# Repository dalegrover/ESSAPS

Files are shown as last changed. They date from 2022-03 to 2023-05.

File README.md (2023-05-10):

# ESSAPS: Experimental Small-Scale Anodizing Power Supply
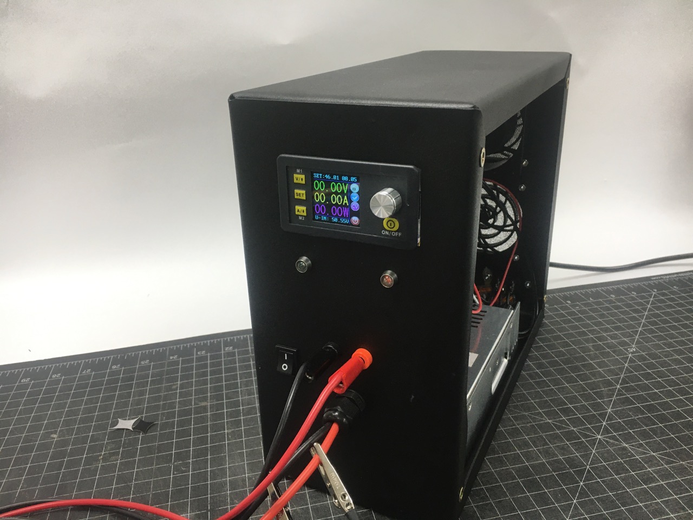
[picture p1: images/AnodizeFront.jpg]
Anodizing power supply front view

The goal of this project is to create an automated power supply to support small-scale anodizing.  By “small-scale”, the output is in the range of 10-15A; this is sufficient for anodizing surfaces of around 1 ft^2 at 12 ASF (amp per sq. ft), or up to around 3 ft^2 at “low current density” (LCD) rates of about 4.5 ASF.
The user interface is via a web page served over WiFi.  The pages are simple HTML--no Javascript, etc.

The power supply is automated and performs the following:
* Given ASF, surface area, ramp time, and target thickness, calculates current, total time, estimated peak voltage, and estimated peak resistance.
* Ramps up the constant current to the target current.
* Stops the current and signals the operator if the time is up or (if enabled) a decrease in resistance is detected (i.e., peak anodizing resistance or PAR).  The latter has been claimed by some to provide a much more reliable method of maximizing layer thickness independent of electrolyte condition, temperature, etc.
* Generates plots in real time of the voltage and current.
* Generates numeric data points for voltage and current (can be copied to a spreadsheet for analysis or plotting).
* By adding a large-valued capacitor and a few low-cost components, the power supply can act as a wire-bonder for bonding aluminum wire to objects to be anodized (i.e., Capacitor-Discharge Welding or CDW, also known in some circles as "sput welding").

This device doesn't do anything that a constant-current power supply plus an attentive person with a calculator can't do.  But, it will do the ramping, timing, and peak resistance detection autonomously, freeing the operator to do other things.

The hardware components of this power supply are:
* 10-15A, 24-50V fixed or variable voltage switching power supply.  A popular brand would be "Mean Well".   24V is likely just sufficient for just anodizing; 48-50V is useful if wire-bonding will be used.
* DPS5015 or DPS5020 Constant-Current/Constant-Voltage buck regulator.  Make sure it supports communication (sometimes sold with a USB converter or Bluetooth, though neither adapter is used for this project).  The DPS3012 will not work--it does not apparently support ModBus.
* ESP-WROOM-32 module.  Make sure the metal shield says "ESP-WROOM-32"--other versions may not work with this code.
* JST-GH 1.25mm 4-pin female cable
* If CDW is desired, a large value (i.e., 0.1 F or more) electrolytic capacitor rated at least 5-10V more than the maximum power supply output, plus a dual relay module.
* Wire, Mini-PV connectors ("DuPont"), AC power switch, circuit breaker, enclosure, fan, fan filters, banana connectors, etc.

The hardware is in a good state.  The software is usable, but needs improvement.

Warning:  This process involves powerful chemicals, high voltage, and the discharge of very high current.  It is critical to use all appropriate safety measures when using this device and process.  The author is not a professional anodizer and may be unaware of other hazards.  Consult a professional before using.  Any use is at your own risk.

See the project wiki for more details:  https://github.com/dalegrover/ESSAPS/wiki

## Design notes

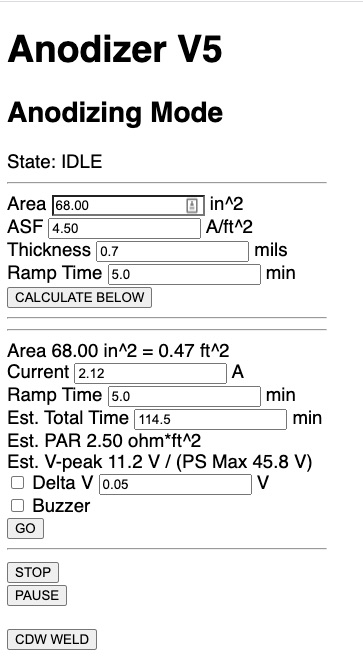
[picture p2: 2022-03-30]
images/webStartPage.jpg

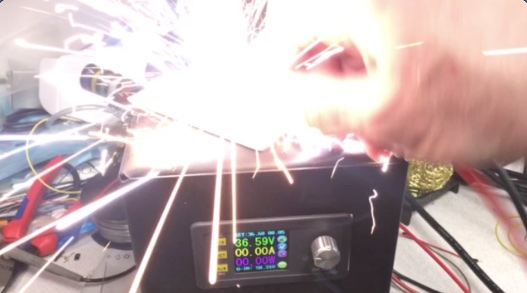
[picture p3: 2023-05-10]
images/CDWThumb.jpg

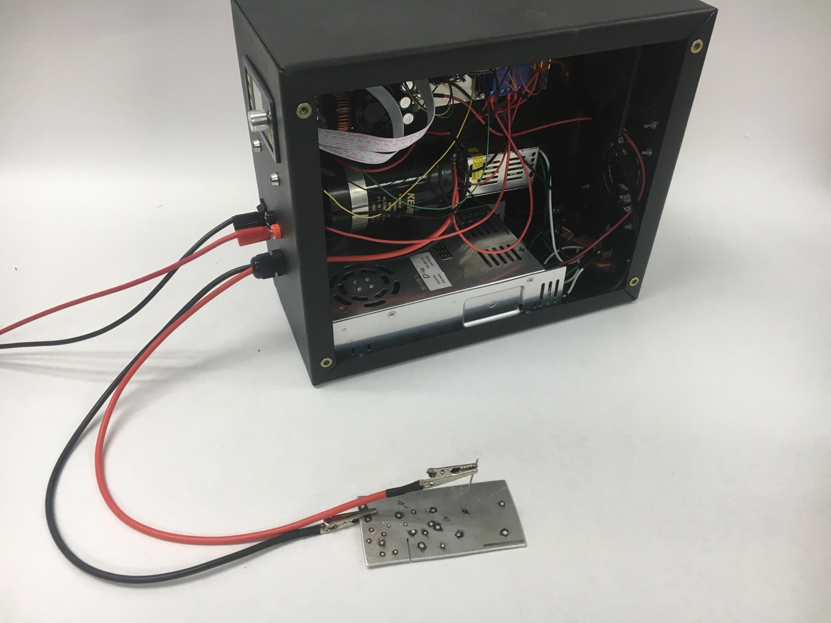
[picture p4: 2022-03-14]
images/AnodizeCDW.jpg

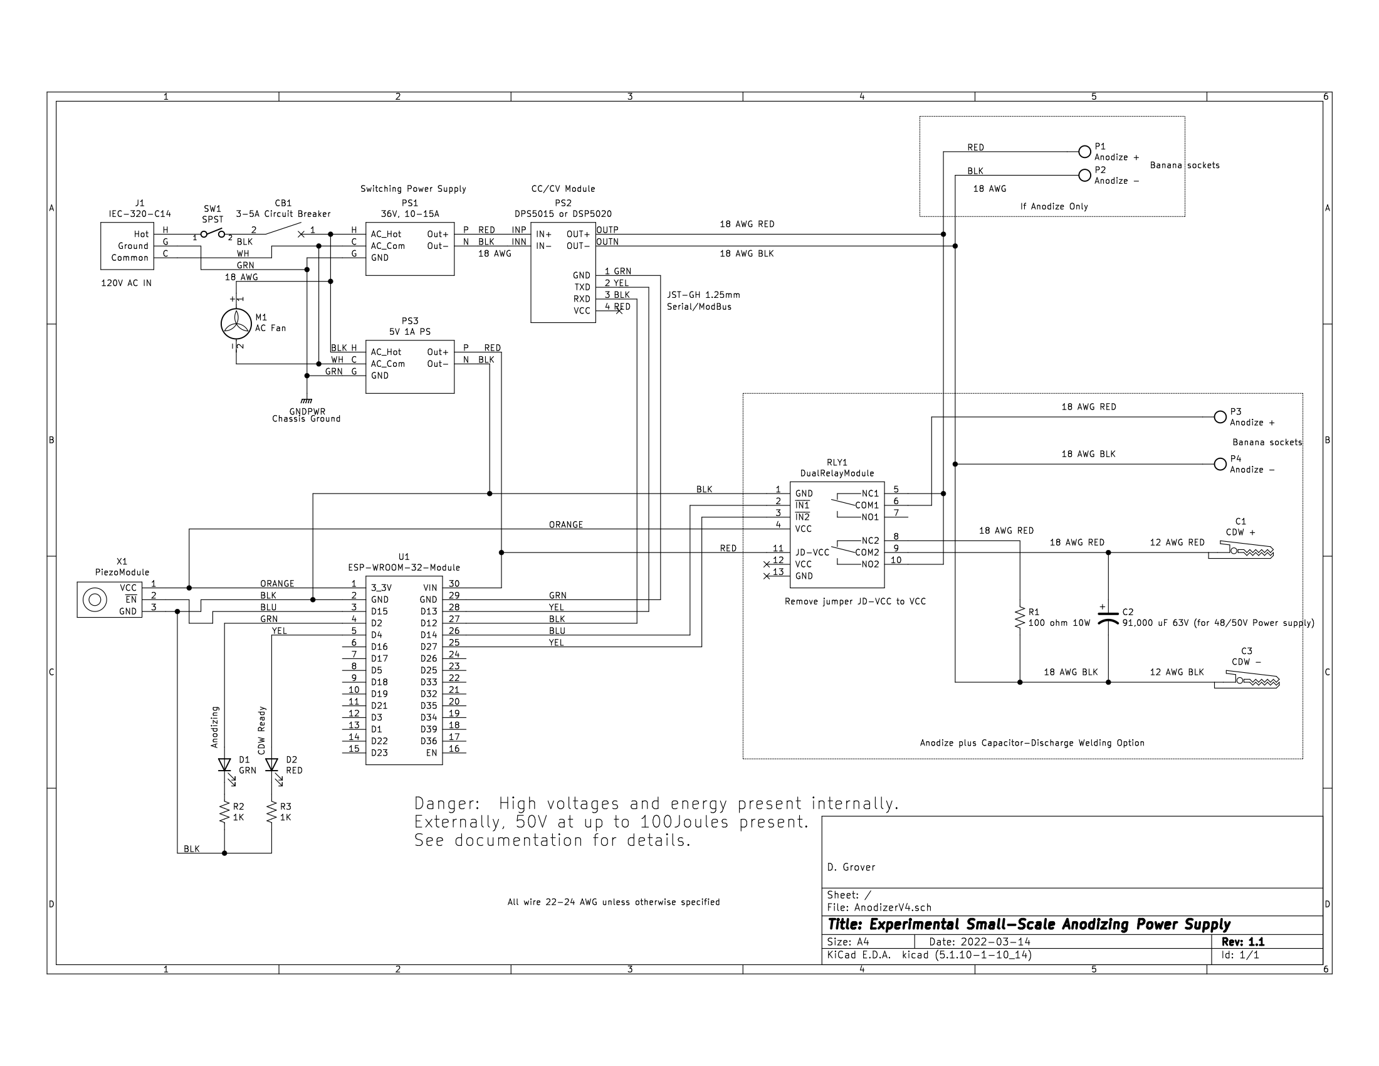
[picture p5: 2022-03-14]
images/AnodizerV4.png

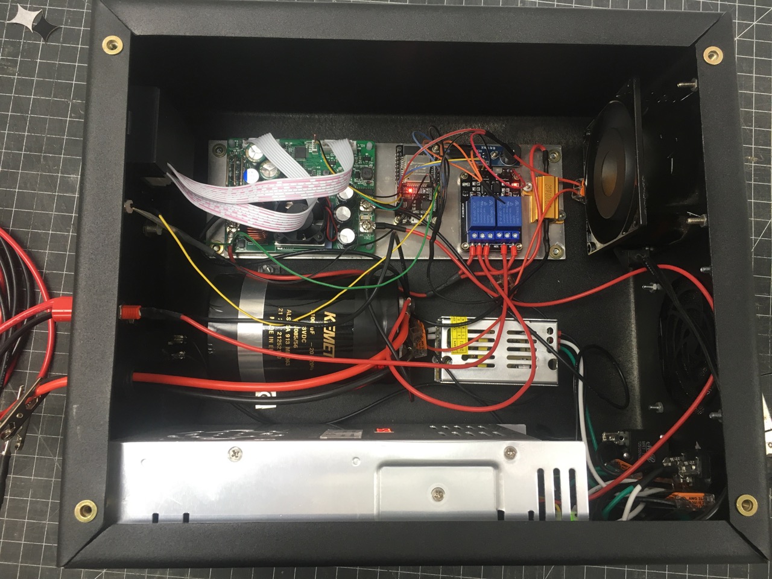
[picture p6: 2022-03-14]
images/AnodizeInside.jpg

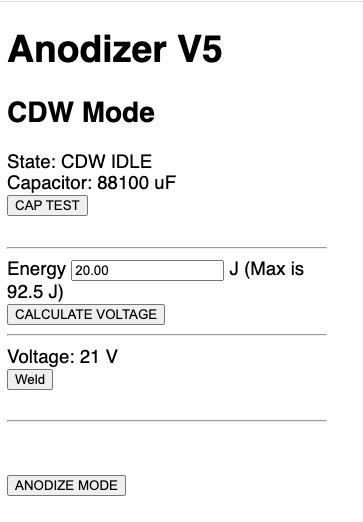
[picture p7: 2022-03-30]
images/webCDWPage.jpg

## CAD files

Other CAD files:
images/Anodizer Enclosure V1 v21.f3d

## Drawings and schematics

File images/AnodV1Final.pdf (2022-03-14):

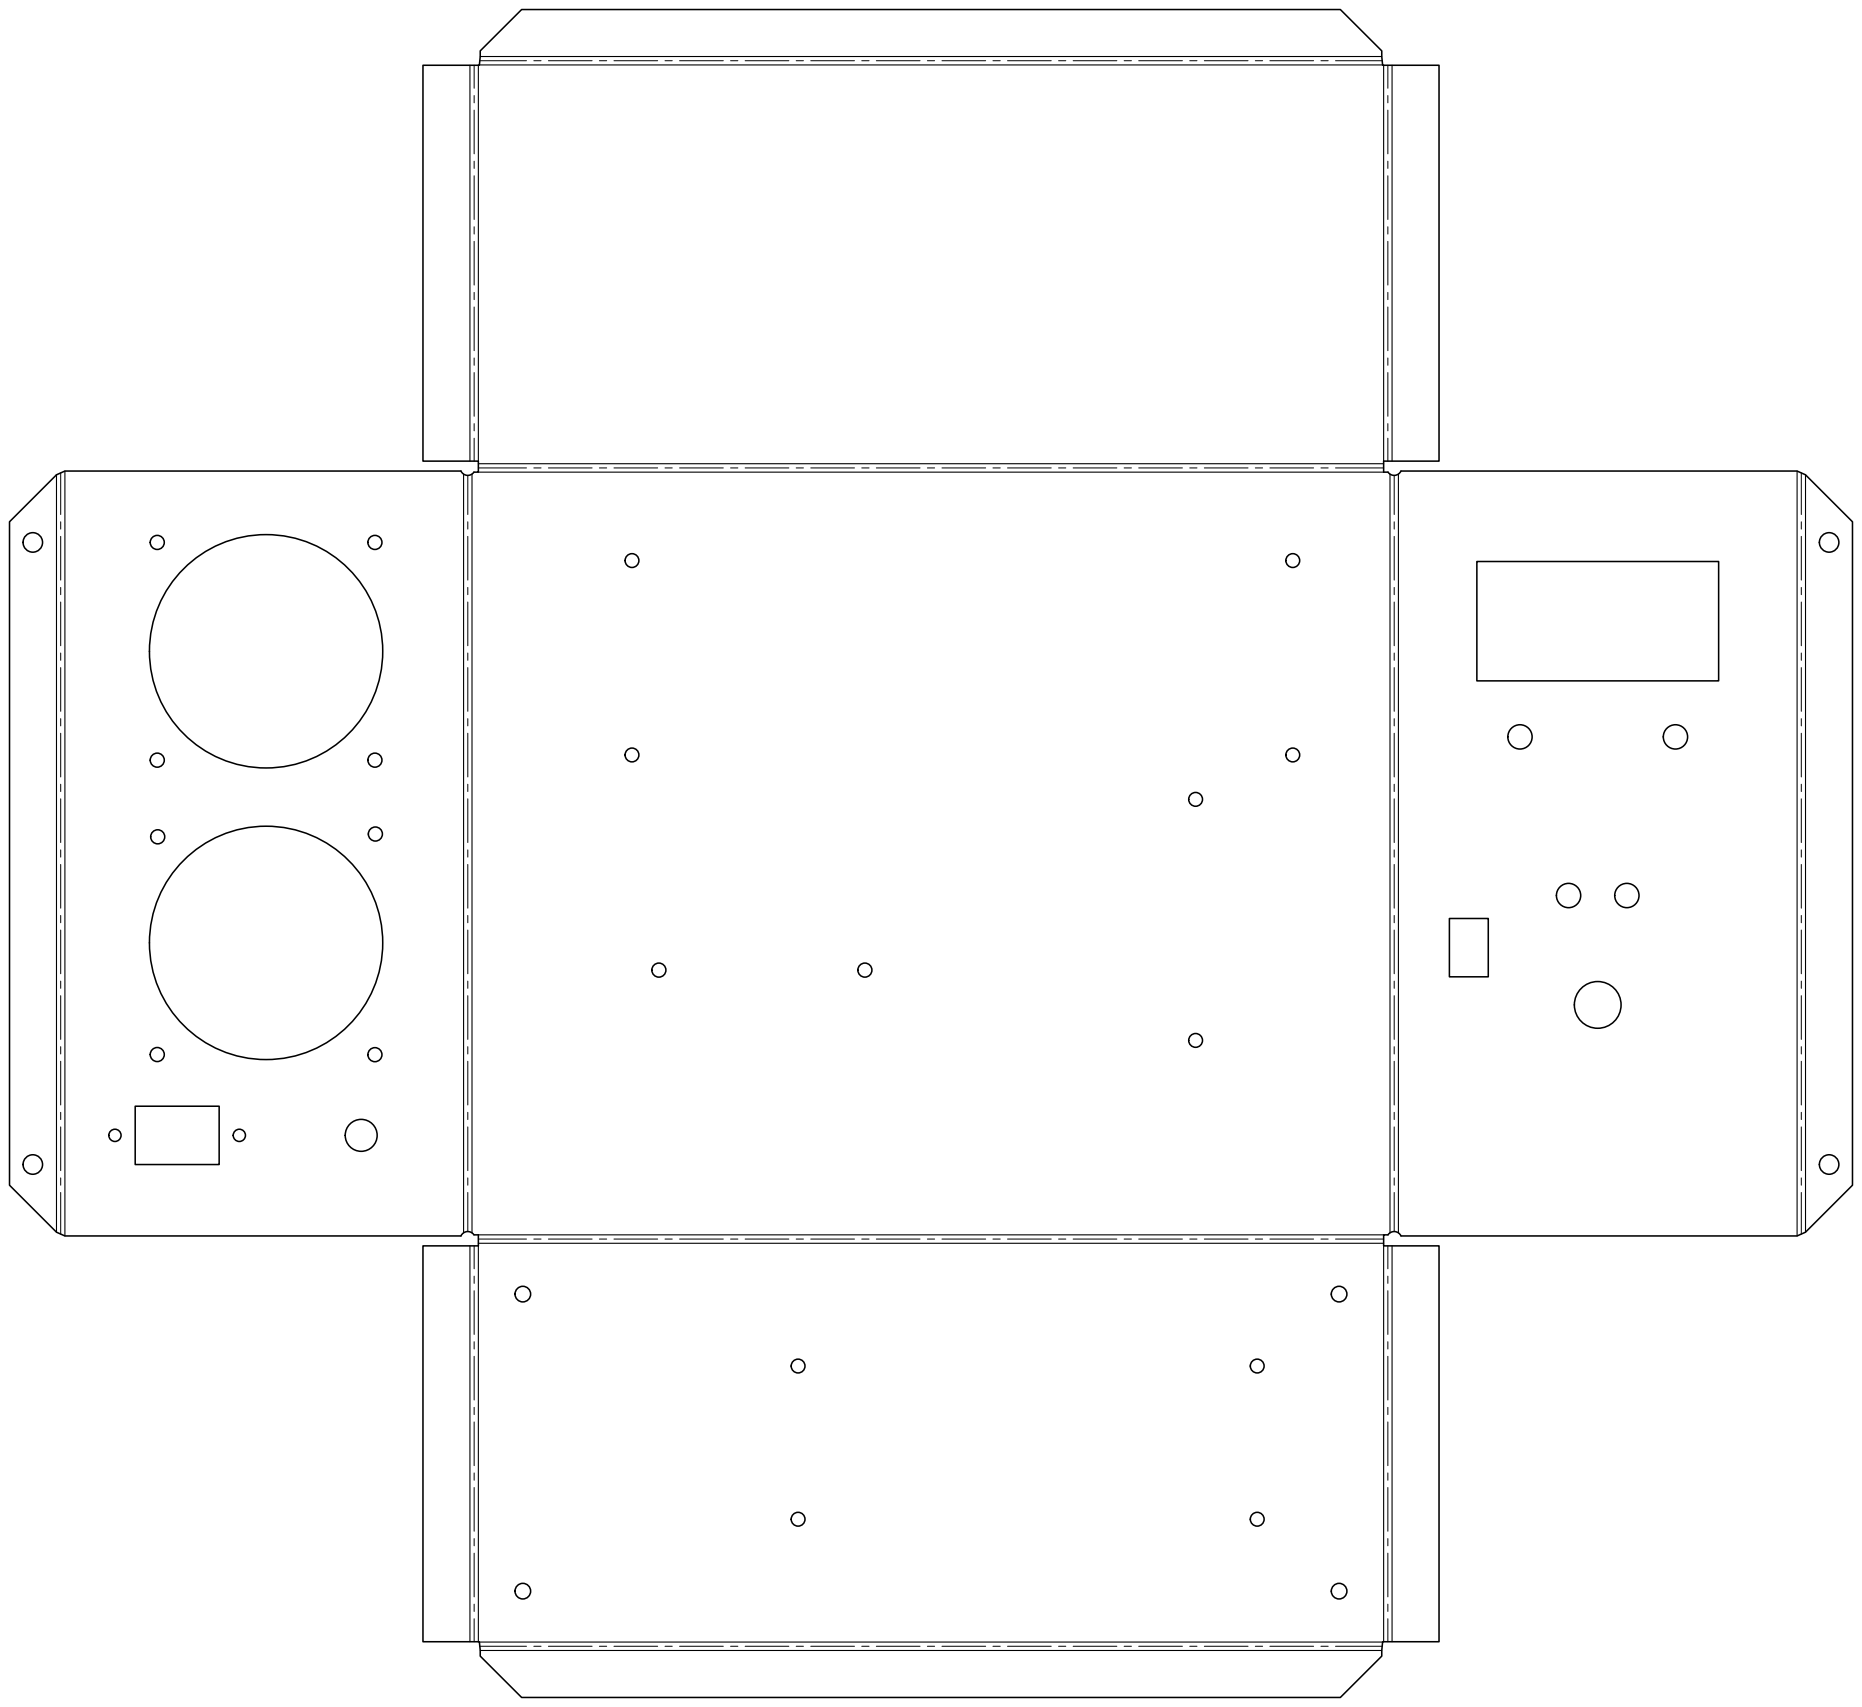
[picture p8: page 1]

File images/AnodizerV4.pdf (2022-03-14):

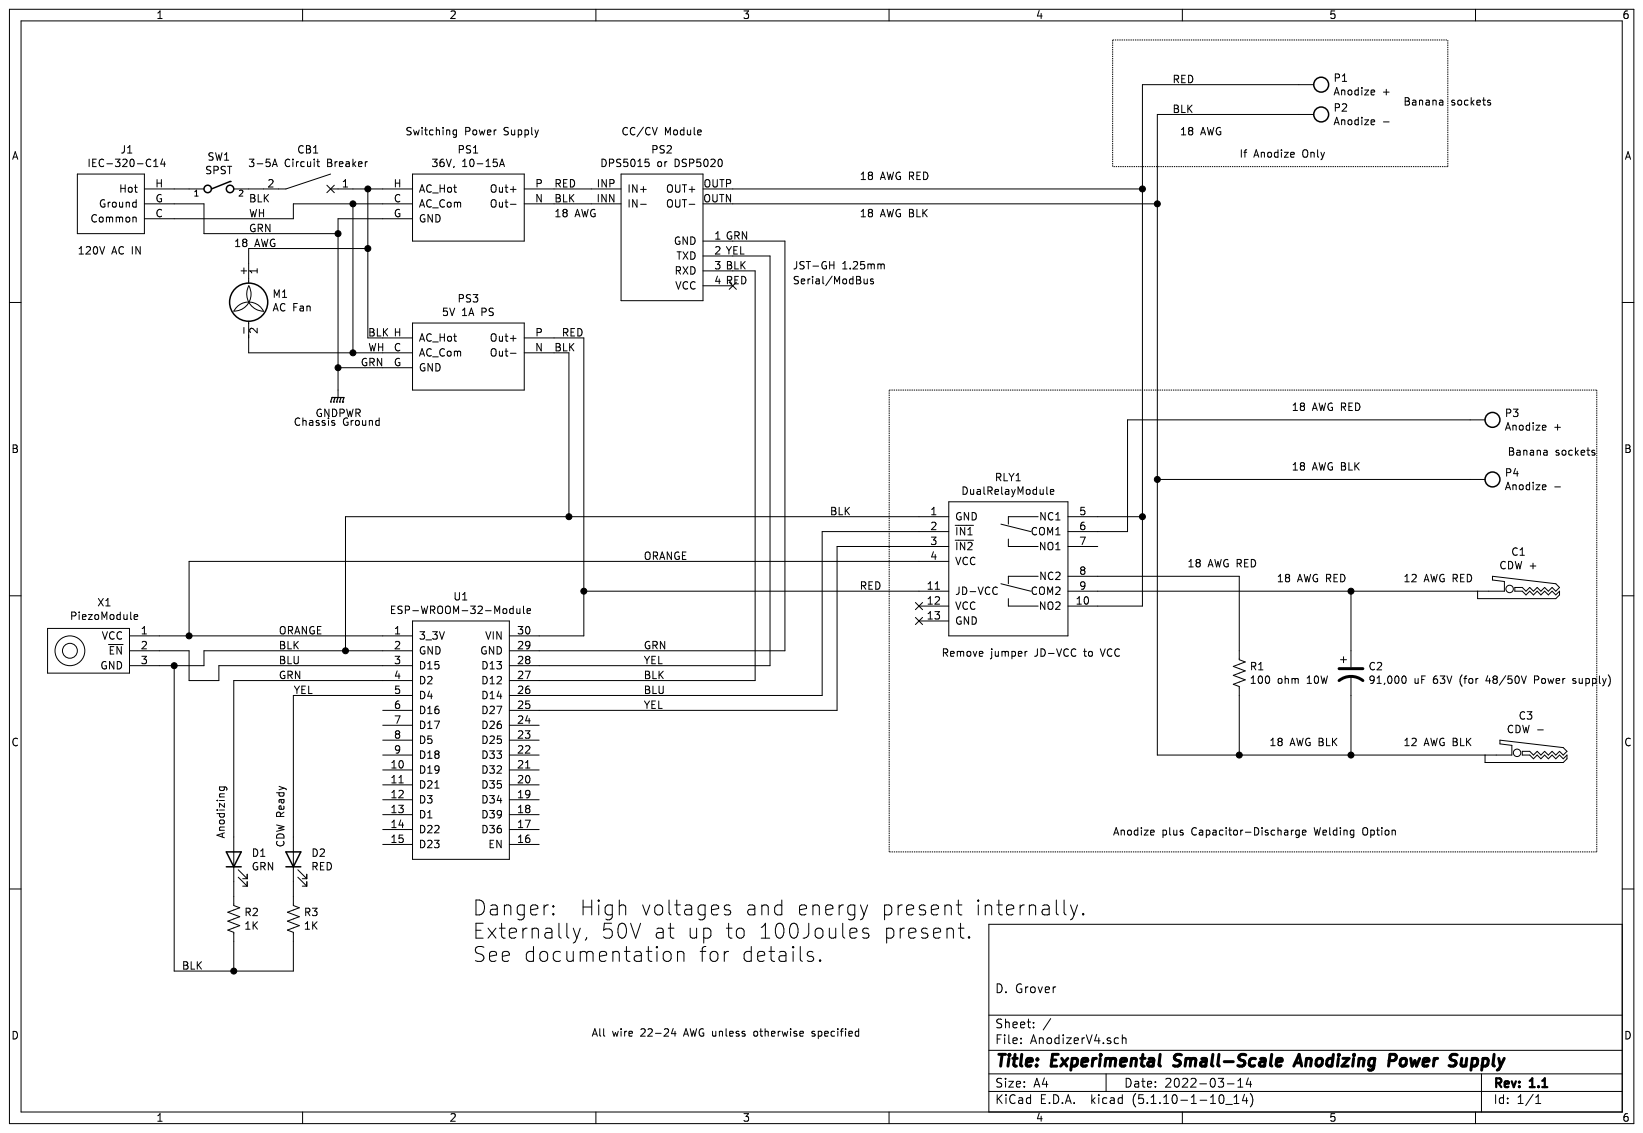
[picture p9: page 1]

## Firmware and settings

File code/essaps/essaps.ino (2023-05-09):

// ESSAPS
// Experimental Small-Scale Anodizing Power Supply
// 5.2
//
// Anodizing power supply and capacitor-discharge welder
// For ESP-WROOM-32 module connected to DPS5015 power supply
// w/ maximum of 50V 15A switching power supply
// Uses ModBus over TTL serial to talk to DPS5015
// TX2 is GPIO 12
// RX2 is GPIO 13
//
// Other I/O:
// GPIO 15:  piezo alarm, active low
// GPIO 2:  Green LED (anodizing active), active high
// GPIO 4:  Red LED (CDW ready to use), active high
// GPIO 13:  RX2 to TXD of DPS5015
// GPIO 12:  TX2 to RXD of DPS5015
// GPIO 14:  relay 1, active low
// GPIO 27:  relay 2, active low

// Relay 1:  hi (default, off) = +Anodize banana socket connected to DPS5015 output
//           lo (active low)   = +Anodize disconnected

// Relay 2:  hi (default, off) = CDW capacitor is discharged through 100 ohm 25W resistor
//           low (active low)  = CDW capacitor is connected to DPS5015 output

// Other connections
// VIN:  +5V in
// GND:  GND
// 3_3V:  Piezo VCC, Relay VCC (remove jumper JD-VCC to VCC, connect +5V to JD-VCC)

//
//  to do:
// if power supply not on, detect and note on web page
// add filtering to the maximum voltage and peak resistance calculation to remove any noise
// ability to save settings (incl. capacitor value)
// make delta v enable persistant, like buzzer
// remove CDW button unless idle/stop/etc.
// more space between buttons & checkboxes
// bold dynamic values


//    Copyright (C) 2021 Dale Grover
//
//
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



#include <WiFi.h>
#include <WebServer.h>

#include "DPS5015.h"

// for debugging without connecting to an actual DPS unit,
// set NO_DPS in DPS5015.h

const char* progVersion = "5.3";

// SSID & Password
const char* ssid = "Anodizer5";  // Enter the SSID here for this device
const char* password = "987654321";  //Enter the password to log on to this device

// IP Address details
IPAddress local_ip(192, 168, 1, 1);
IPAddress gateway(192, 168, 1, 1);
IPAddress subnet(255, 255, 255, 0);

WebServer server(80);  // Object of WebServer(HTTP port, 80 is defult)

float anodizingAreaIn; // area in sq inches, all surfaces
float anodizingAreaFt; // anodizingAreaIn / 144, in sq ft
float anodizingCurrent; // 0.050A to 15A, float
float anodizingRampTime; // minutes
float anodizingMaxTime; // minutes
float anodizingPAR; // peak anodizing resistance (ohm sq ft)
float anodizingVPeak; // Volts, estimated peak voltage
float anodizingASF; // amp/sq ft
float anodizingThickness; // mils
float anodizingPeakRSF; // peak resistance per sq ft
float anodizingDeltaV; // change in V to signal end of cycle
int anodizingEnableDeltaV; // true or false to enable delta V end of cycle
float anodizingMaxV; // actual maximum voltage so far during CC

// CDW welding
float CDWCapacitance; // capacitance in Farads
float CDWEnergy; // energy per weld in Joules
float CDWVoltage; // voltage to give CDWEnergy given CDWCapacitance

// web page status string
char *statusString; // points to a status string--e.g., "Timed out"
char statusBuffer[50]; // in case you need a dynamic status--like "Delta V at 32.7 seconds"
char timeBuffer[20]; // for time, for above

int piezoEnable; // enable buzzer at end of anodizing cycle

// set max voltage to about 5 volts less than input voltage to DPS5015
float maxVoltage;

// second UART (to DPS5015 using modbus)
#define RXD2 13
#define TXD2 12

// piezo buzzer (active, active low) on GPIO15
#define PIEZO 15
#define PIEZO_OFF 1
#define PIEZO_ON 0

// LEDs
#define LED_ANODIZE 2
#define LED_CDW 4
#define LED_ON 1
#define LED_OFF 0

// relays
#define RELAY_1 14
#define RELAY_2 27
#define RELAY_ON 0
#define RELAY_OFF 1

#define BUFLEN 50


// States
#define STATE_IDLE 0
#define STATE_START 1
#define STATE_PAUSE 2
#define STATE_PAUSED 3
#define STATE_RAMP 4
#define STATE_CC 5
#define STATE_DONE 6
#define STATE_TIMED_OUT 7
#define STATE_STOP 8
#define STATE_STOPPED 9
#define STATE_DELTA_V 10
#define STATE_CDW_IDLE 11
#define STATE_TEST_CAP 12
#define STATE_CDW_STOP 13
#define STATE_CDW_CHARGE 14
#define STATE_CDW_CHARGING 15
#define STATE_CDW_READY 16
#define STATE_CDW_WAIT_TO_RESET 17


char *stateNames[] = {"IDLE", "START", "PAUSE", "PAUSED", "RAMP", "CONSTANT CURRENT", "DONE", \
                      "TIMED OUT", "STOP", "STOPPED", "DELTA-V HALT", "CDW IDLE", "TEST CAP", \
                      "CDW STOP", "CDW CHARGE", "CDW CHARGING", "CDW READY", "CDW WAIT TO RESET" \
                     };

int state;
int pauseState;

// data arrays, for 3 hours at 12 samples/minute (5 secs/sample)
#define ARRAY_HOURS 3
#define ARRAY_SAMPLES_PER_MINUTE 12
#define MAX_READINGS (ARRAY_HOURS * 60 * ARRAY_SAMPLES_PER_MINUTE)
float readingsCurrent[MAX_READINGS];
float readingsVoltage[MAX_READINGS];
int readingIndex;

void setup()
{
  // set up piezo
  pinMode(PIEZO, OUTPUT);
  digitalWrite(PIEZO, PIEZO_OFF);

  // set up LEDs
  pinMode(LED_ANODIZE, OUTPUT);
  pinMode(LED_CDW, OUTPUT);
  digitalWrite(LED_ANODIZE, LED_OFF);
  digitalWrite(LED_CDW, LED_OFF);

  // set up relays
  pinMode(RELAY_1, OUTPUT);
  pinMode(RELAY_2, OUTPUT);
  digitalWrite(RELAY_1, RELAY_ON); // disconnect anodize socket
  digitalWrite(RELAY_2, RELAY_OFF); // discharge CDW capacitor

  // serial via USB to host computer
  Serial.begin(115200);
  // serial to DSP5015 power supply (modbus)
  // factory default is 9600, can go to 19200
  Serial2.begin(9600, SERIAL_8N1, RXD2, TXD2);

  delay(4000); // let things settle (was 5000)

  // set to defaults, disable outputs
  setModBusRegVerified(REG_ONOFF_SET, 0); // 0=off, disable output
  // now calculate maximum output voltage, which is Vout = Vin/1.1
  maxVoltage = getModBusReg(REG_VIN_READ) / 100.0 / 1.1;
  setModBusRegVerified(REG_V_SET, int(maxVoltage * 100)); // set MAX_VOLTAGE * 100
  setModBusRegVerified(REG_I_SET, 5); // set 00.05A, minimal current

  // set up web server
  // Create SoftAP
  WiFi.disconnect(); // these 3 lines important:  https://github.com/espressif/arduino-esp32/issues/2025
  WiFi.mode(WIFI_OFF);
  delay(1000);
  WiFi.persistent(false);
  WiFi.softAP(ssid, password);
  delay(2000); // this delay is "very important"--bug in kernal?
  WiFi.softAPConfig(local_ip, gateway, subnet);

  Serial.print("\n\n----------------\nAnodizer v");
  Serial.print(progVersion);
  Serial.print("\n----------------\n");
  Serial.print("Access point: ");
  Serial.println(ssid);
  Serial.println(password);

  Serial.print("Maximum Voltage:  ");
  Serial.println(maxVoltage);

  // we only serve two things: the main page and the svg plot
  server.on("/", handle_root);
  server.on("/graph.svg", graphvi);
  server.onNotFound(handleNotFound);

  server.begin();
  Serial.println("HTTP server started");

  state = STATE_IDLE;
  statusString = "Idle";

  // defaults
  anodizingAreaIn = 144.0; // area in inches (total, all surfaces/sides)
  anodizingASF = 4.5; // for LCD (low current density anodizing), 6 ASF and below
  anodizingThickness = 0.7; // 0.0007" = 0.7 mils thickness
  anodizingRampTime = 5; // default ramp time in minutes
  anodizingDeltaV = 0.05; // change in V to halt cycle (if enabled)
  anodizingEnableDeltaV = false;
  calculateParams();

  // CDW capacitor--this is default, but can test and set programmatically too
  CDWCapacitance = 0.091; // 91,000 uF
  CDWEnergy = 20.0; // 20J, default energy per weld
  calculateCDWVoltage();

  // Energy in CDW capacitor is 1/2 C V^2
  // For 45V and 90,000 uF (0.09F), E=91J.
  // (It so happens that at 45V, E in J is the C in MFD)

  piezoEnable = false; // no buzzer at end by default
  digitalWrite(PIEZO, PIEZO_OFF);

} // setup()


// given area, ASF, thickness, and ramp time, calculate
// current, time, est PAR, est VPeak

// This array maps ASF to PAR
// May need adjusting for sodium bifsulfate; may not be accurate.
// Some folks just use 0.95 ohm for everything, but I believe that may apply at high ASF
// 0 to 24 ASF
float ASFtoPAR[] = {5.00, 4.00, 3.00, 2.67, 2.50, 2.33, 2.17, 2.09, 2.00, 1.92, 1.84, 1.75, 1.67, 1.61, 1.55, 1.49, 1.43, 1.37, 1.31, 1.25, 1.19, 1.13, 1.07, 1.01, 0.95};

void calculateParams()
{
  // convert to sq feet
  anodizingAreaFt = anodizingAreaIn / 144.0;

  // find current
  anodizingCurrent = anodizingAreaFt * anodizingASF;

  // find approx peak anodizing resistance
  if ( anodizingASF > 23.0)
    anodizingASF = 23.0;
  anodizingPAR = ASFtoPAR[ (int) anodizingASF ];

  // find est. peak voltage
  anodizingVPeak = anodizingPAR * anodizingASF;

  // find time, in minutes ("720 rule")
  anodizingMaxTime = 720.0 * anodizingThickness / anodizingASF;
  // ramp time is on average 1/2 current, so add 1/2 ramp time
  anodizingMaxTime += anodizingRampTime / 2;
}


// given capacitance & energy, find voltage required
void calculateCDWVoltage()
{
  CDWVoltage = sqrt( CDWEnergy * 2 / CDWCapacitance);
  if (CDWVoltage > maxVoltage)
  {
    // requested energy requires too high voltage; drop down to maxVoltage
    CDWVoltage = maxVoltage;
    CDWEnergy = CDWCapacitance * CDWVoltage * CDWVoltage / 2.0;
  }
}

float startTime;  // in seconds (converted from millis)
int lastTime; // seconds, in int, last time through



// log readings to arrays
void logReadings(void)
{
  float voltage, current;
  float currentTime;

  // check if time for record sample
  currentTime = getSeconds();
  if ( ((int)currentTime == lastTime) || ( (int)currentTime % 5 != 0) )
  {
    lastTime = (int) currentTime;
    return;  // return if we haven't processed this
  }
  lastTime = (int) currentTime;

  // debug only
  Serial.println(readingIndex);

  voltage = (float)(getModBusReg(REG_V_READ)) / 100.0;
  current = (float)(getModBusReg(REG_I_READ)) / 100.0;

  readingsCurrent[readingIndex] = current;
  readingsVoltage[readingIndex] = voltage;

  readingIndex++;
  if (readingIndex >= MAX_READINGS)
    readingIndex = MAX_READINGS - 1;
  return;
}


// return mean value of last n points
float meanPoints(int n)
{
  int first, last, i;
  float sum = 0.0;
  first = readingIndex - n;
  if ( first < 1)
    return (0.0);
  if ( n == 0)
    return (0.0);
  for (i = 0; i < n; i++)
  {
    sum += readingsVoltage[i + first];
  }
  return ( sum / n);
}


float getSeconds(void)
{
  return ( millis() / 1000.0 );
}


// beep for one second
void beep()
{
  digitalWrite(PIEZO, PIEZO_ON);
  delay(1000);
  digitalWrite(PIEZO, PIEZO_OFF);
}


void loop()
{
  float currentTime; // in seconds (converted from millis)
  float current; // current reading
  float voltage;  // output voltage reading
  int setCurrent;

  server.handleClient();

  currentTime = getSeconds();

  switch (state)
  {
    case STATE_IDLE:
      // nothing to do
      // make sure LEDs and relays in default state
      digitalWrite(LED_ANODIZE, LED_OFF);
      digitalWrite(LED_CDW, LED_OFF);
      digitalWrite(RELAY_1, RELAY_ON); // disconnect anodize socket
      digitalWrite(RELAY_2, RELAY_OFF); // discharge CDW capacitor
      break;

    case STATE_START:
      int setc, setv;
      startTime = getSeconds(); // set start time for anodizing cycle
      // set the voltage to max, set current as given, turn on output
      setc = 0; // start current out at zero for ramp
      setv = int( maxVoltage * 100.0);
      setModBusRegVerified(REG_V_SET, setv); // voltage
      setModBusRegVerified(REG_I_SET, setc); // current
      setModBusRegVerified(REG_ONOFF_SET, 1); // 1=on, enable output
      anodizingPeakRSF = 0.0; // max resistance per sq ft, reset
      anodizingMaxV = 0.0; // max voltage, reset
      state = STATE_RAMP;
      statusString = "Ramping";
      // turn on anodizing LED
      digitalWrite(LED_ANODIZE, LED_ON);
      digitalWrite(RELAY_1, RELAY_OFF); // connect anodize socket
    // fall through to ramp state

    // ramping up
    case STATE_RAMP:
      logReadings();
      // calculate current for now
      currentTime = getSeconds(); // time since start in seconds
      if ( (currentTime - startTime) >= (anodizingRampTime * 60.0) )
      {
        // set to full current
        setCurrent = int( anodizingCurrent * 100.0);
        setModBusRegVerified(REG_I_SET, setCurrent);
        state = STATE_CC;
        statusString = "Constant Current Mode";
        break;
      }
      current = ((currentTime - startTime) / (anodizingRampTime * 60.0) ) * anodizingCurrent;
      // update power supply current
      setCurrent = int( current * 100.0);
      setModBusRegVerified(REG_I_SET, setCurrent);
      break;

    // constant current state--actively anodizing, hasn't reached peak or timed out
    case STATE_CC:
      logReadings();
      // time up?
      currentTime = getSeconds(); // time since start in seconds
      if ( (currentTime - startTime) >= anodizingMaxTime * 60)
      {
        setModBusRegVerified(REG_I_SET, 0);  // turn off current
        setModBusRegVerified(REG_ONOFF_SET, 0); // disable output
        state = STATE_TIMED_OUT;
        statusString = "Timed Out";
        // turn off LED
        digitalWrite(LED_ANODIZE, LED_OFF);
        if (piezoEnable)
          beep();
        break;
      }

      // read voltage, set if maximum
      voltage = (float)(getModBusReg(REG_V_READ)) / 100.0;
      if ( voltage > anodizingMaxV)
      {
        anodizingMaxV = voltage;
      }

      // check for peak
      //
      if (anodizingEnableDeltaV == true)
      {
        if ( voltage + anodizingDeltaV <= anodizingMaxV)
        {
          setModBusRegVerified(REG_I_SET, 0);  // turn off current
          setModBusRegVerified(REG_ONOFF_SET, 0); // disable output
          state = STATE_DELTA_V;
          // turn off LED
          digitalWrite(LED_ANODIZE, LED_OFF);
          timeString(timeBuffer, (int)currentTime);
          sprintf(statusBuffer, "Peak Resistance at %s", timeString);
          statusString = statusBuffer;
          if (piezoEnable)
            beep();
          break;
        }
      }
      break;

    case STATE_DELTA_V:
      // just hang out here
      break;

    case STATE_DONE:
      // just hang out here
      break;

    case STATE_TIMED_OUT:
      // just hang out here
      break;

    case STATE_PAUSE:
      setModBusRegVerified(REG_I_SET, 0);  // turn off current
      setModBusRegVerified(REG_ONOFF_SET, 0); // disable output
      pauseState = state; // capture the state pause is hit in
      state = STATE_PAUSED;
      if ( pauseState == STATE_RAMP)
        statusString = "Pause during ramp";
      else
        statusString = "Pause during constant current";
    // fall thru

    case STATE_PAUSED:
      // later on, add resume button
      // can check pauseState to find what state to return to
      break;

    case STATE_STOP:
      setModBusRegVerified(REG_I_SET, 0);  // turn off current
      setModBusRegVerified(REG_ONOFF_SET, 0); // disable output
      state = STATE_STOPPED;
      statusString = "Stop button pressed";
      // make sure LEDs and relays in default state
      digitalWrite(LED_ANODIZE, LED_OFF);
      digitalWrite(LED_CDW, LED_OFF);
      digitalWrite(RELAY_1, RELAY_ON); // disconnect anodize socket
      digitalWrite(RELAY_2, RELAY_OFF); // discharge CDW capacitor
    // fall thru

    case STATE_STOPPED:
      // just hang out here until a new cycle
      break;

    // tests capacitor value, sets to CDWCapacitance
    case STATE_TEST_CAP:
      {
        digitalWrite(RELAY_1, RELAY_ON); // disconnect anodize socket
        digitalWrite(RELAY_2, RELAY_ON); // connect CDW capacitor to power supply
        // turn off output
        setModBusRegVerified(REG_ONOFF_SET, 0); // disable output
        // set voltage to max output voltage
        setModBusRegVerified(REG_V_SET, int(maxVoltage * 100) ); // set voltage
        // set current to 0.1A
        setModBusRegVerified(REG_I_SET, 10);  // current to 00.10A
        // turn on output
        setModBusRegVerified(REG_ONOFF_SET, 1); // enable output
        // wait 5 seconds
        delay(5000);
        // get voltage
        float voltage;
        voltage = (float)(getModBusReg(REG_V_READ)) / 100.0;
        // turn off output
        setModBusRegVerified(REG_ONOFF_SET, 0); // disable output
        digitalWrite(RELAY_2, RELAY_OFF); // discharge CDW capacitor
        // calculate capacitance
        // C = 1/V * 0.1 * 5, in farads
        // C = 1/V * current * time

        CDWCapacitance = (1.0 / voltage) * 0.1 * 5.0;
      }
      state = STATE_CDW_IDLE;
      break;

    case STATE_CDW_IDLE:
      // CDW welding idle state
      digitalWrite(RELAY_1, RELAY_ON); // disconnect anodize socket
      digitalWrite(RELAY_2, RELAY_OFF); // discharge CDW capacitor
      digitalWrite(LED_CDW, LED_OFF);
      break;

    // start charging
    case STATE_CDW_CHARGE:
      Serial.print("CDW charge...");
      digitalWrite(RELAY_1, RELAY_ON); // disconnect anodize socket
      digitalWrite(RELAY_2, RELAY_ON); // CDW capacitor to power supply
      startTime = getSeconds(); // debug!!
      // turn off output
      setModBusRegVerified(REG_ONOFF_SET, 0); // disable output
      // set voltage
      setModBusRegVerified(REG_V_SET, (int)(CDWVoltage * 100));
      // set current to 1A--just an arbitrary rate, should be less than 5 seconds to full charge at 1F 50V
      setModBusRegVerified(REG_I_SET, 100);  // current to 01.00A
      // turn on output
      setModBusRegVerified(REG_ONOFF_SET, 1); // enable output
      Serial.print(" done in "); // debug
      Serial.println( getSeconds() - startTime);
      state = STATE_CDW_CHARGING;
      startTime = getSeconds(); // set start time for anodizing cycle
      break;

    case STATE_CDW_CHARGING:
      // have we been charging too long?
      currentTime = getSeconds(); // time since start in seconds
      if ( (currentTime - startTime) >= 15.0 ) // 15 seconds max
      {
        // should give some other error indication or suggestion to correct
        // this probably is a short circuit
        setModBusRegVerified(REG_ONOFF_SET, 0); // disable output
        state = STATE_CDW_IDLE;
        break;
      }
      // wait for voltage to get within 0.5V of set voltage
      voltage = (float)(getModBusReg(REG_V_READ)) / 100.0;
      if ( voltage + 0.5 >= CDWVoltage )
      {
        // switch over to 0.05A
        setModBusRegVerified(REG_I_SET, 5);  // current to 0.050A (the smallest supported)
        state = STATE_CDW_READY;
        digitalWrite(LED_CDW, LED_ON); // CDW ready LED
      }
      break;

    // ready, wait for short to bring to zero
    case STATE_CDW_READY:
      voltage = (float)(getModBusReg(REG_V_READ)) / 100.0;
      if ( voltage < 1.0 )
      {
        // set output voltage to 2V (still at 0.050A)
        setModBusRegVerified(REG_V_SET, 200);  // voltage to 02.00 V
        state = STATE_CDW_WAIT_TO_RESET;
        digitalWrite(LED_CDW, LED_OFF); // turn off CDW LED
      }
      break;

    // wait for voltage to go above 1V--i.e., open circuit, so can charge again
    case STATE_CDW_WAIT_TO_RESET:
      voltage = (float)(getModBusReg(REG_V_READ)) / 100.0;
      if ( voltage > 1.0 )
      {
        state = STATE_CDW_CHARGE;
      }
      break;

    case STATE_CDW_STOP:
      // turn off output
      setModBusRegVerified(REG_ONOFF_SET, 0); // disable output
      state = STATE_CDW_IDLE;
      digitalWrite(LED_CDW, LED_OFF);
      break;


    default:
      state = STATE_IDLE;



  } // switch(state)


} // loop()



// returns the argument index matching the name,
// or -1 if no match
int getArgWithName(char *name)
{
  for ( uint8_t i = 0; i < server.args(); i++)
  {
    if ( server.argName(i) == name)
      return (i);
  }
  return (-1);
}
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

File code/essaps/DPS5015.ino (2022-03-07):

// ModBus
// modbus:  16-bit data:  high/low (big-endian)
//          16-bit crc:   low/high using CRC below
// for long discussion, see https://control.com/forums/threads/byte-order-of-modbus-crc.11616/


//    The function CRC16_2() is used under Creative Commons Attribution-ShareAlike 4.0 International License.
//
//    The remainder is
//    Copyright (C) 2021 Dale Grover
//
//
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


#include "DPS5015.h"

// address: default of DPS5015 is 0x0001
#define MODBUS_ADDRESS 0x01

// read register(s)
#define FUNCTION_READ 0x03

// write single register
#define FUNCTION_WRITE 0x06

// model, r
#define REG_MODEL 0x000b

// version, r
#define REG_VERSION 0x000c

#ifdef NO_DPS
unsigned int fakeRegs[50];
#endif


// set the modbus register, but verify it was set by reading.
// if okay, return 1, if not, return 0
unsigned int setModBusRegVerified(unsigned int reg, unsigned int val)
{
  unsigned int rv;

  rv=setModBusReg(reg,val);
  if(rv==0xffff)
  {
    Serial.print("Error writing ");
    Serial.print(val);
    Serial.print(" to register ");
    Serial.println(reg);
    return(0);
  }
  // now verify it took
  rv=getModBusReg(reg);
  if( rv == val)
  {
    return(1); // okay!
  }
  else
  {
    Serial.print("Error writing ");
    Serial.print(val);
    Serial.print(" to register ");
    Serial.print(reg);
    Serial.print(" actually read back ");
    Serial.println(rv);
    return(0);
  }
} // setModBusRegVerified()


// Simulate DPS?
#ifdef NO_DPS

unsigned int setModBusReg(unsigned int reg, unsigned int val)
{
  fakeRegs[reg]=val;
  return(val);  
}

#else

// sets modbus register to value
// returns 0xffff if error, else returns value returned by DSP5015
unsigned int setModBusReg(unsigned int reg, unsigned int val)
{
  //                     addr           write          regh regl valh vall crch crcl
  unsigned char buf[20] = { MODBUS_ADDRESS, FUNCTION_WRITE, 0xFF, 0xFF, 0xff, 0xff};
  int len;

  buf[2] = reg >> 8; // register high
  buf[3] = reg & 0xff; // register low
  buf[4] = val >> 8; // value high
  buf[5] = val & 0xff; // value low

  makeModBus(buf, 6); // len will be 8 with crc appended
  sendModBus(buf, 8); // send it
  len = getModBus(buf, 20); // get up to 20 chars back
  // but should get exactly 8 back
  if (len != 8)
  {
    printf("\n");
    for (int i = 0; i < len; i++)
    {
      printf("%02x ", buf[i]);
    }
    printf("\n");
    return (0xffff); // error
  }
  // addr, write, regh, regl, valh, vall, crch, crcl
  return ( (buf[5] << 8) + buf[6] );
} // setModBusReg()

#endif


// simulate DPS?
#ifdef NO_DPS

unsigned int getModBusReg(unsigned int reg)
{
  if( reg == REG_V_READ )
    return( readingIndex * 15 / 12 * 100);
  if( reg == REG_I_READ )
    return( fakeRegs[REG_I_SET] );
  return( fakeRegs[reg] );
}


#else

// returns 16-bit register value of reg or ffff for error
unsigned int getModBusReg(unsigned int reg)
{
  //                      addr read regh regl cnth cntl crch crcl
  unsigned char buf[20] = { MODBUS_ADDRESS, FUNCTION_READ, 0xFF, 0xFF, 0x00, 0x01};
  int len;

  buf[2] = reg >> 8; // register high
  buf[3] = reg & 0xff; // register low
  makeModBus(buf, 6); // len will be 8 with crc appended
  sendModBus(buf, 8); // send it
  len = getModBus(buf, 20); // get up to 20 chars back
  if (len != 7)
  {
    printf("\n");
    for (int i = 0; i < len; i++)
    {
      printf("%02x ", buf[i]);
    }
    printf("\n");
    return (0xffff); // error
  }
  // addr, read, bytesRead, regh, regl, crch, crcl
  return ( (buf[3] << 8) + buf[4] );
} // getModBusReg()

#endif


// sends out serial 2
int sendModBus(unsigned char *buf, int len)
{
  for (int i = 0; i < len; i++)
    Serial2.write(buf[i]);
} // sendModBus()


// get serial response until timeout
// or maxLen of buffer is met
// returns number of bytes read
int getModBus(unsigned char *buf, int maxLen)
{
  int i;
  int timeout;
  int done;

  timeout = 0; // in msecs
  done = false;
  while (!done)
  {
    if (Serial2.available())
      done = true;
    delay(1); // 1 msec
    timeout++;
    if (timeout > 500)
      return (0); // timed out waiting for initial transmission
  }

  i = 0; // count of bytes received
  timeout = 0;
  while (true)
  {
    if (i >= maxLen)
      return (i);

    if (Serial2.available())
    {
      buf[i] = Serial2.read();
      i++;
      timeout = 0; // reset timer
    }
    else
    {
      delay(1); // 1 msec
      timeout++;
      if (timeout > 10)
      {
        return (i); // timed out, last char received
      }
    }
  } // while(true)
  return (i); // should never get here...
}

// given the modbus data in a buffer that has room for 2 more chars,
// generate CRC and append.  returns length
int makeModBus(unsigned char *buf, int len)
{
  unsigned int crc, crcHigh, crcLow;
  crc = CRC16_2(buf, len);
  crcHigh = crc >> 8;
  crcLow = crc & 0xff;
  buf[len + 1] = crcHigh;
  buf[len] = crcLow;
  return (len + 2);
}



// from https://stackoverflow.com/questions/19347685/calculating-modbus-rtu-crc-16
// The following function is licensed under a Creative Commons Attribution-ShareAlike 4.0 International License.
unsigned int CRC16_2(unsigned char *buf, int len)
{
  unsigned int crc = 0xFFFF;
  for (int pos = 0; pos < len; pos++)
  {
    crc ^= (unsigned int)buf[pos];    // XOR byte into least sig. byte of crc

    for (int i = 8; i != 0; i--)
    { // Loop over each bit
      if ((crc & 0x0001) != 0)
      { // If the LSB is set
        crc >>= 1;                    // Shift right and XOR 0xA001
        crc ^= 0xA001;
      }
      else                            // Else LSB is not set
        crc >>= 1;                    // Just shift right
    } // for i
  } // for pos

  return crc;
}

// examples:
/*
    // go through registers
    printf("Registers\n");
    printf("V-set:  %0.2f\n", float(getModBusReg(REG_V_SET)) / 100.0 );
    printf("I-set:  %0.2f\n", float(getModBusReg(REG_I_SET)) / 100.0 );
    printf("V-read:  %0.2f\n", float(getModBusReg(REG_V_READ)) / 100.0 );
    printf("I-read:  %0.2f\n", float(getModBusReg(REG_I_READ)) / 100.0 );
    printf("On/Off:  %04x\n", getModBusReg(REG_ONOFF_SET) );
    printf("CVCC:  %04x\n", getModBusReg(REG_CVCS_READ) );

    delay(1000);
    setModBusReg(REG_ONOFF_SET, 0); // 0=off, disable output

    setModBusReg(REG_V_SET, 2300); // set 23.00V
    setModBusReg(REG_I_SET, 0005); // set 00.05A

    // go through registers
    printf("Registers\n");
    printf("V-set:  %0.2f\n", float(getModBusReg(REG_V_SET)) / 100.0 );
    printf("I-set:  %0.2f\n", float(getModBusReg(REG_I_SET)) / 100.0 );
    printf("V-read:  %0.2f\n", float(getModBusReg(REG_V_READ)) / 100.0 );
    printf("I-read:  %0.2f\n", float(getModBusReg(REG_I_READ)) / 100.0 );
    printf("On/Off:  %04x\n", getModBusReg(REG_ONOFF_SET) );
    printf("CVCC:  %04x\n", getModBusReg(REG_CVCS_READ) );

 */

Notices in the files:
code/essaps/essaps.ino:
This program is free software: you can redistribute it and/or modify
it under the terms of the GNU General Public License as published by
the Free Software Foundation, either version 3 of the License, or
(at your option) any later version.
